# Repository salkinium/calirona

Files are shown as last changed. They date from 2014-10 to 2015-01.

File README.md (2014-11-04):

# Calirona: A calibration robot for Corona

The [Corona][corona] headphones use a HMC6343 compass for heading information which needs to be calibrated from time to time.
To do this, a robot rotates the headphones around two axis while the compass is in calibration mode.

The main design goals of this project are to:

-	calibrate the compass,
-	minimize the required technical knowledge to operate the robot,
-	test the compass functionality to catch the most obvious malfunctions.

This project was designed and manufactured at [The Media Computing Group][i10].

## Design

The robot can move the headphones around both two axes a full 360°, which are supported using ball bearings. The z-axis uses a dish which holds the headphones.

Since the power and signal lines for the headphones and second axis motor need to be relayed through both axis, the robot cannot rotate infinitely around its axis.  
Therefore two position switches exist, which allow the robot to rotate its axes into known safe positions before attempting a rotation.  
The robot will then rotate 360° around the x-axis, then 360° around the z-axis, and then reverse all rotations until it has reached the starting state again.

The robot is controlled by two buttons Start and Stop, and can display its internal state through leds for power, busy, headphone error and mechanical error.  
The mapping is as follows:

- START: initialize and start the calibration.
- STOP: stop robot movement (short press), release motors and reset robot (long press)
- Busy (blue): blinks, when an operation is in progress, otherwise off
- Headphone (orange): blinks, when no headphone is connected, or it is unresponsive (perhaps broken), otherwise on
- Mechanical Error (red): blinks, when the robot detected an invalid mechanical state (broken or blocked motor), otherwise off

## Usage

The basic usage of the robots is as follows:

1. Plug in the power cord. The green power led should light up and the headphone error led should blink.
2. Place the headphone into the holder drum and plug in the headphone jack. The headphone error led should stop blinking and turn on fully, unless the headphone is broken.
3. Press START. The robot will initialize its axes.
4. Press START again. The robot will do two rotations while calibrating the headphones.
5. Once the robot stopped moving, unplug the now calibrated headphones and remove them.

If the robot detected an invalid state during any of the actions, it will stop moving and blink an error led.

**Press the STOP button anytime to stop the robot from moving!**  
Pressing the STOP button for a longer time resets the robot.

## Organization

This repository is organized as follows:

- 	The *hardware* folder contains all hardware files for the robot.
	-	*hardware/et* contains the PCB schematics and layouts.
	-	*hardware/mech* contains the vector files of all mechanical parts of the robot (for the lasercutter).
- 	The *software* folder contains the software for the robot.
	- 	*software/source* contains the actual application code for this robot.
	-	*software/xpcc* contains the git submodule for the xpcc.io microcontroller framework.

All hardware and embedded software was designed by [Niklas Hauser][hauser].

[i10]: http://hci.rwth-aachen.de
[corona]: http://hci.rwth-aachen.de/corona
[hauser]: http://hci.rwth-aachen.de/hauser

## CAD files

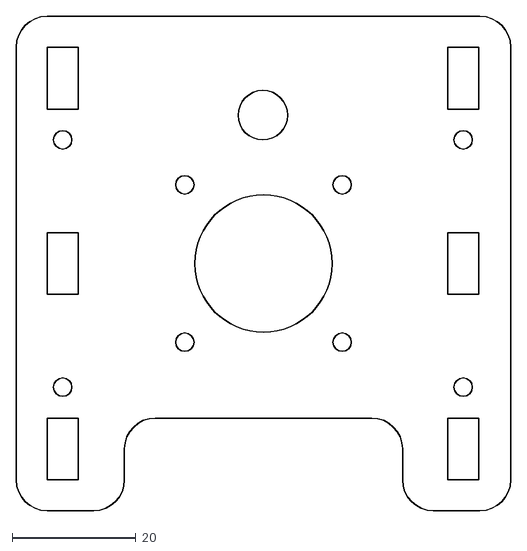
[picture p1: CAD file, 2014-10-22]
hardware/mech/gears_x_large_without_gear_5mm.dxf
80.0 x 80.0

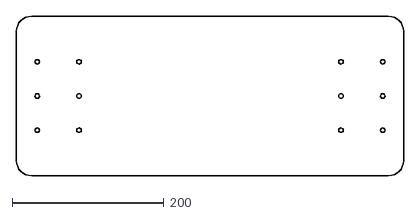
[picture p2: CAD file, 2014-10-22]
hardware/mech/base_large.dxf
510.0 x 210.0

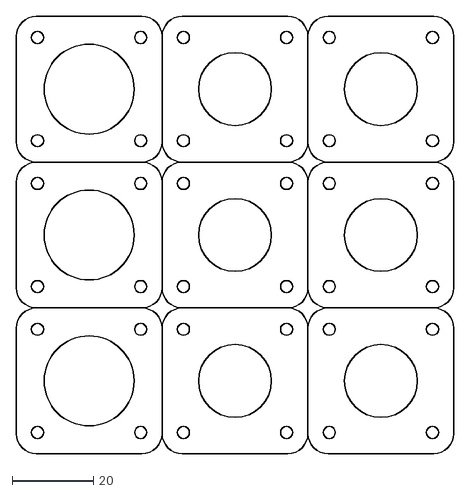
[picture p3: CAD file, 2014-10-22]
hardware/mech/gears_z_center_bearing_holder_2mm.dxf
108.0 x 108.0

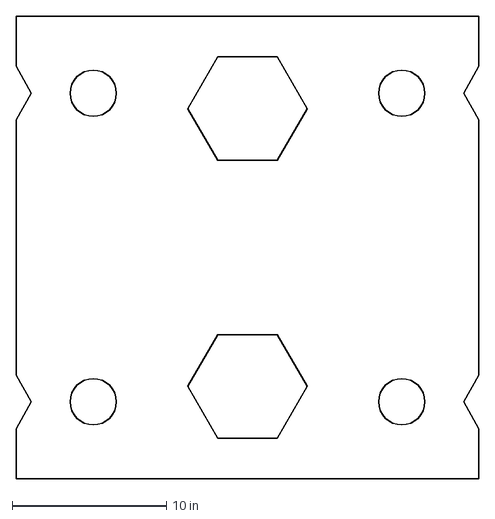
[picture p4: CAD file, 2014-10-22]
hardware/mech/rotation_arm_side_holder_bearings_upper.dxf
30.0 x 30.0 in

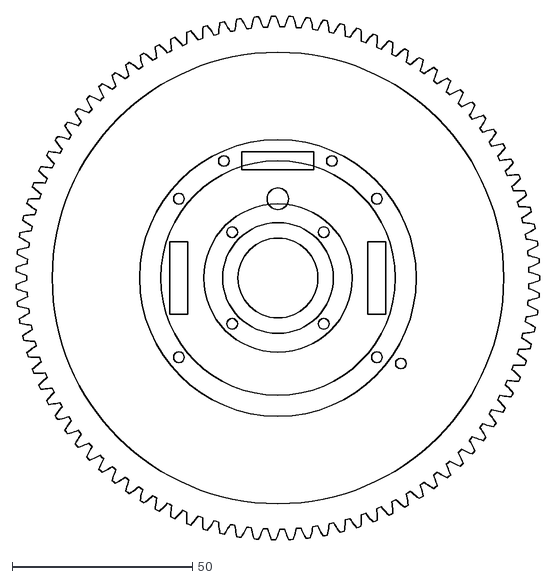
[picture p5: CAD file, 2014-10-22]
hardware/mech/gears_z_large_5mm.dxf
145.5 x 145.5

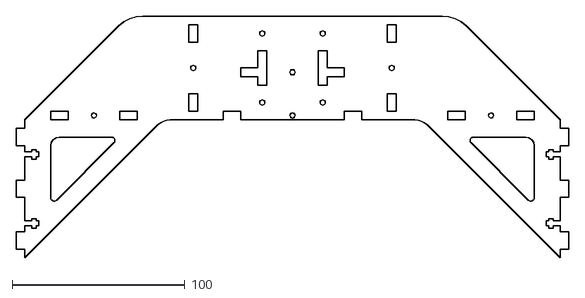
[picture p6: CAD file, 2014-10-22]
hardware/mech/rotation_arm.dxf
320.0 x 140.0

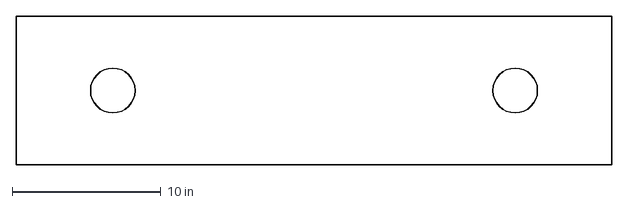
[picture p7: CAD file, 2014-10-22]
hardware/mech/rectphones.dxf
40.0 x 10.0 in

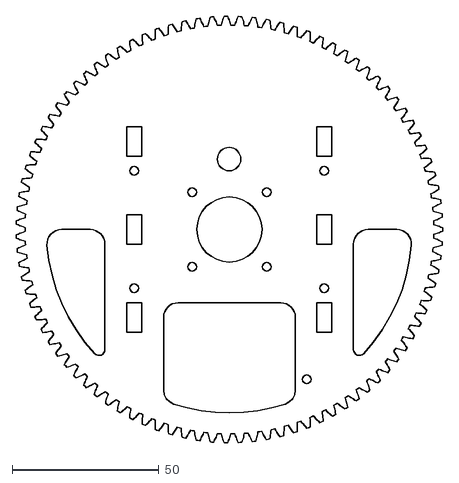
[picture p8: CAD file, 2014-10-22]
hardware/mech/gears_x_large_5mm.dxf
145.5 x 145.5

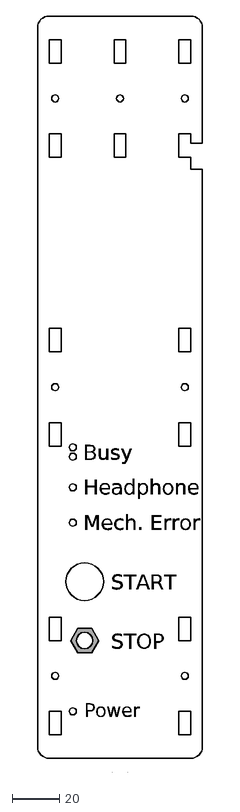
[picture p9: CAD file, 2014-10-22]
hardware/mech/arm_side_structure_LEDs.dxf
Power
Mech. Error
Headphone
Busy
START
STOP

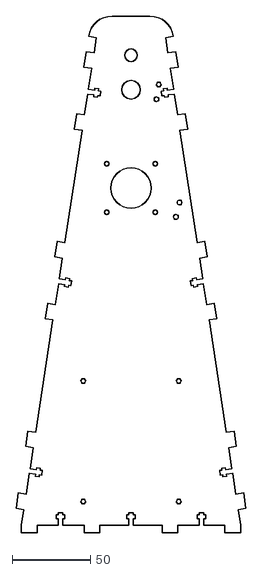
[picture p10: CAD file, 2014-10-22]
hardware/mech/arm_structure_motor.dxf
146.8 x 330.0

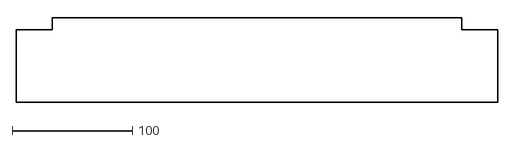
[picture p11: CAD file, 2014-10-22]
hardware/mech/holder_drum_circumfence.dxf
400.0 x 70.0

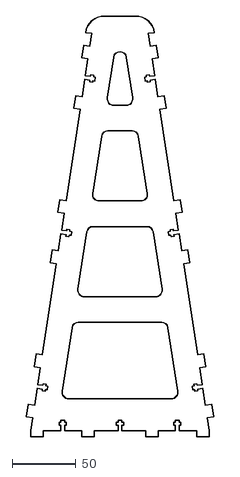
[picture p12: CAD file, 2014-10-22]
hardware/mech/arm_structure.dxf
146.8 x 330.0

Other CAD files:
hardware/mech/rotation_arm_side_holder_stabilizer.dxf
hardware/mech/holder_drum_bottom_5mm.dwg
hardware/mech/arm_axis_middle.dxf
hardware/mech/rotation_arm_side_holder.dxf
hardware/mech/holder_vertical_5mm.dwg
hardware/mech/holder_drum_top_5mm.dxf
hardware/mech/arm_axis_middle.dwg
hardware/mech/arm_side_structure.dwg
hardware/mech/arm_side_structure.dxf
hardware/mech/arm_side_structure_LEDs.dwg
hardware/mech/arm_structure.dwg
hardware/mech/arm_structure_axis.dwg
hardware/mech/arm_structure_axis.dxf
hardware/mech/arm_structure_motor.dwg
hardware/mech/base_large.dwg
hardware/mech/base_small.dwg
hardware/mech/base_small.dxf
hardware/mech/gears_x_large_5mm.dwg
hardware/mech/gears_x_large_without_gear_5mm.dwg
hardware/mech/gears_z_center_bearing_holder_2mm.dwg
hardware/mech/gears_z_large_5mm.dwg
hardware/mech/gears_z_small_5mm.dwg
hardware/mech/gears_z_small_5mm.dxf
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

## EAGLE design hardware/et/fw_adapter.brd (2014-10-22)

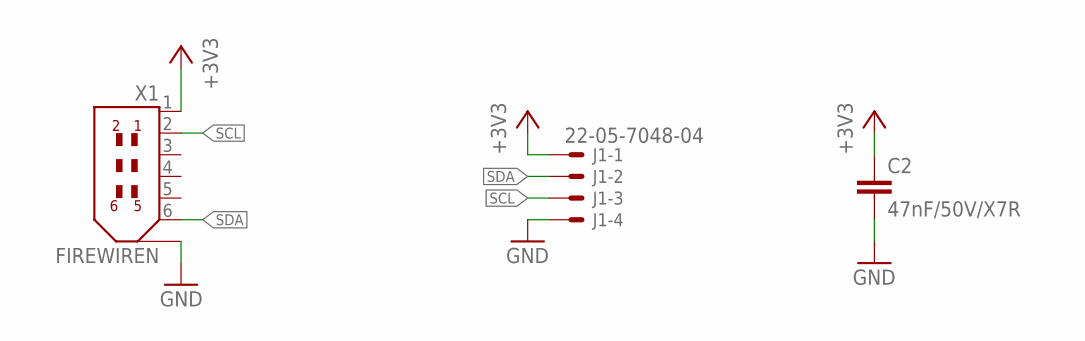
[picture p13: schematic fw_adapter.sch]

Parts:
C2: 47nF/50V/X7R; C0603K
J1: 22-05-7048-04; 7395-04
X1: FIREWIREN; IEEE1394_90DEG_PINS_NORMAL

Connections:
+3V3: C2.1, J1.1, X1.1
GND: C2.2, J1.4, X1.M1 (7), X1.M2 (7)
SCL: J1.3, X1.2
SDA: J1.2, X1.6

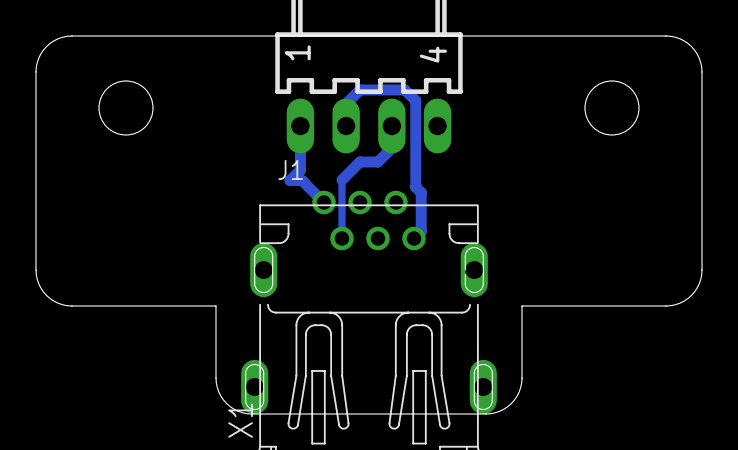
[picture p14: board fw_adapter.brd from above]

Board: 2 copper layers, 37.0 x 21.0 mm, 3 parts (1 on the bottom side), 4 nets.

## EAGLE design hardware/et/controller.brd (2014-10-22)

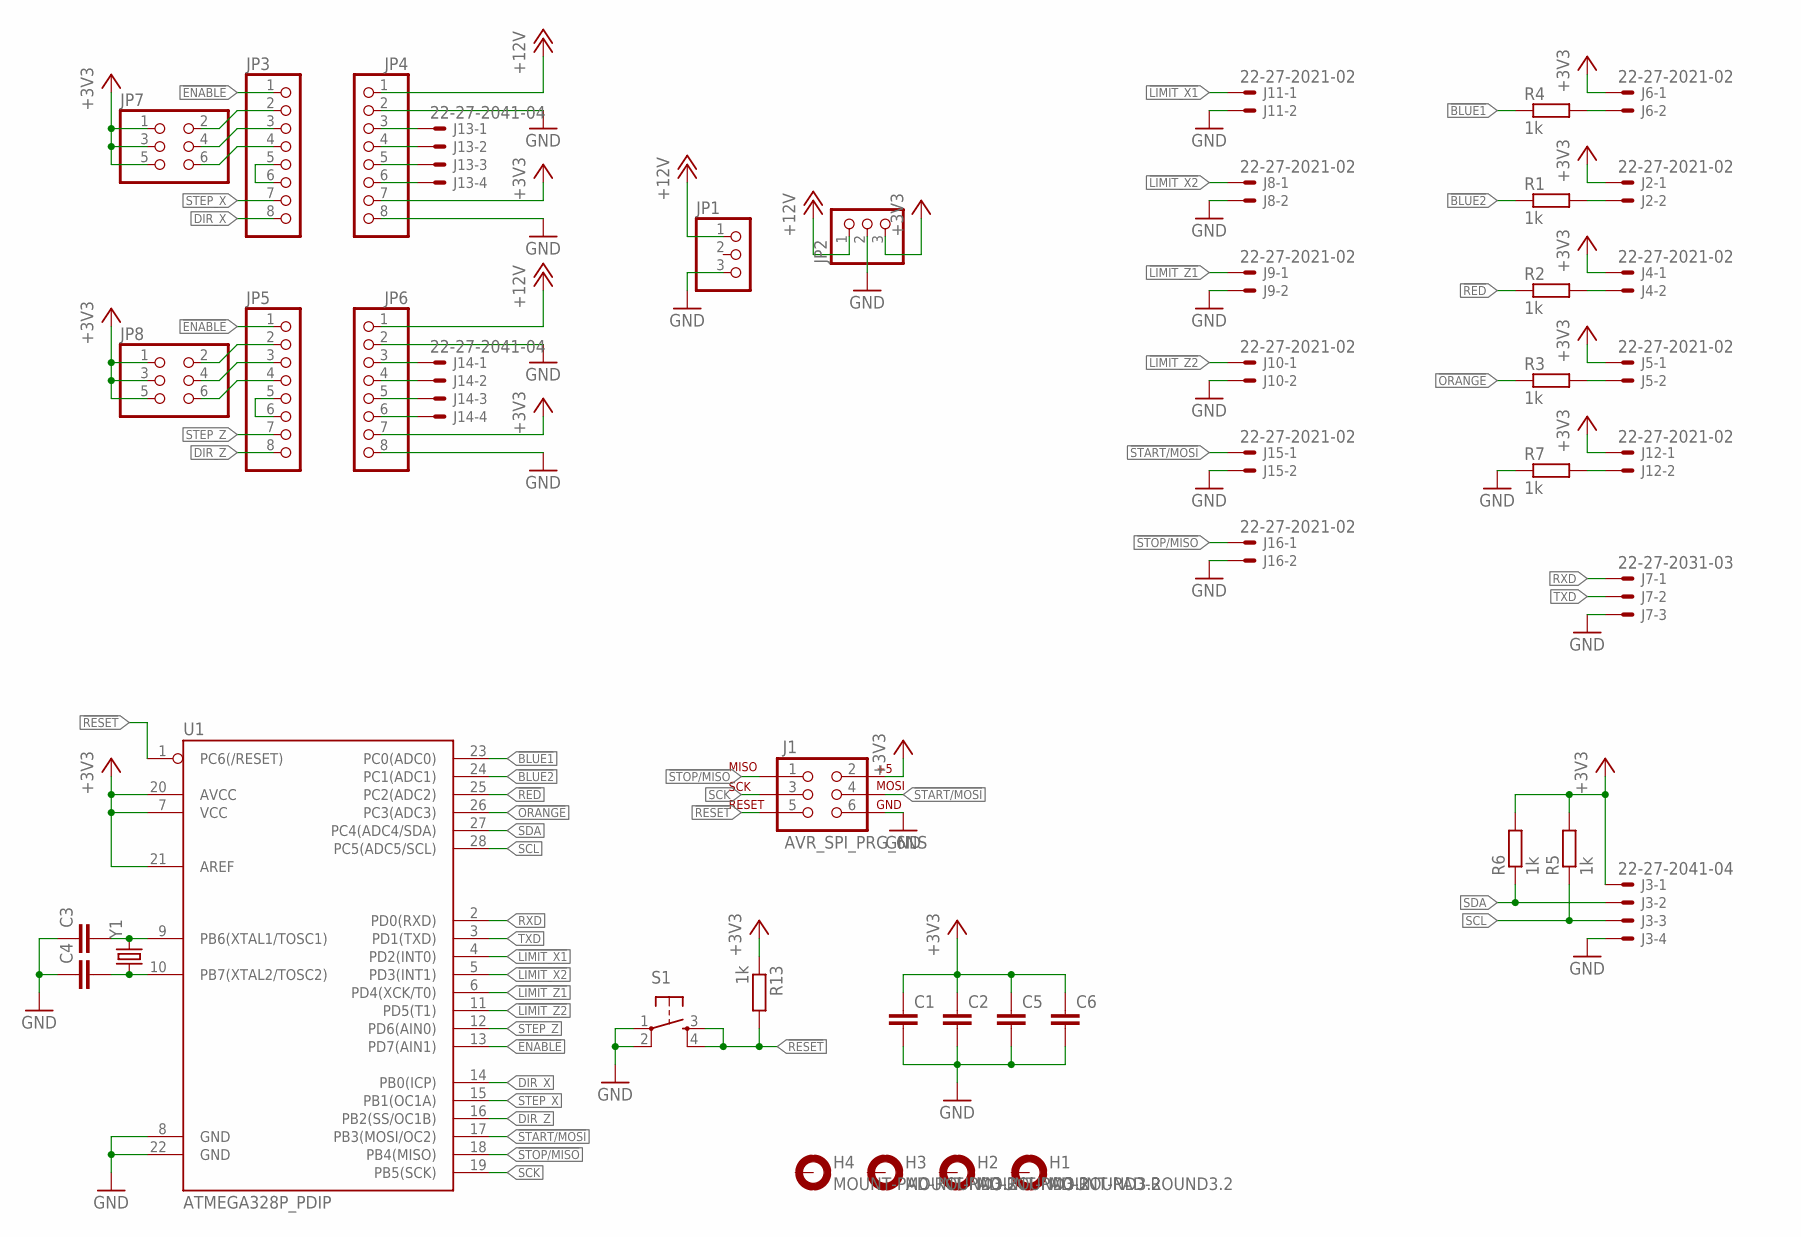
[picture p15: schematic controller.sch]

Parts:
C1, C2, C5, C6: C-EUC0603; C0603
C3, C4: C-EUC0603K; C0603K
H1, H2, H3, H4: MOUNT-PAD-ROUND3.2; 3,2-PAD
J1: AVR_SPI_PRG_6NS; 2X3-NS
J2, J4, J5, J6, J8, J9, J10, J11, J12, J15, J16: 22-27-2021-02; 6410-02
J3, J13, J14: 22-27-2041-04; 6410-04
J7: 22-27-2031-03; 6410-03
JP1, JP2: PINHD-1X3; 1X03
JP3, JP4, JP5, JP6: PINHD-1X8; 1X08
JP7, JP8: PINHD-2X3; 2X03
R1, R2, R3, R4, R5, R6, R7, R13: 1k; R0603
S1: TAC_SWITCHPTH; TACTILE-PTH
U1: ATMEGA328P_PDIP; DIL28-3
Y1: CRYSTALHC49UV; HC49U-V

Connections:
!BLUE1: R4.1, U1.23 (PC0(ADC0))
!BLUE2: R1.1, U1.24 (PC1(ADC1))
!ENABLE: JP3.1, JP5.1, U1.13 (PD7(AIN1))
!LIMIT_X1: J11.1, U1.4 (PD2(INT0))
!LIMIT_X2: J8.1, U1.5 (PD3(INT1))
!LIMIT_Z1: J9.1, U1.6 (PD4(XCK/T0))
!LIMIT_Z2: J10.1, U1.11 (PD5(T1))
!ORANGE: R3.1, U1.26 (PC3(ADC3))
!RED: R2.1, U1.25 (PC2(ADC2))
!RESET: J1.5, R13.2, S1.3, S1.4, U1.1 (PC6(/RESET))
!START/MOSI: J1.4, J15.1, U1.17 (PB3(MOSI/OC2))
!STOP/MISO: J1.1, J16.1, U1.18 (PB4(MISO))
+3V3: C1.1, C2.1, C5.1, C6.1, J1.2, J2.1, J3.1, J4.1, J5.1, J6.1, J12.1, JP2.3, JP4.7, JP6.7, JP7.1, JP7.3, JP7.5, JP8.1, JP8.3, JP8.5, R5.2, R6.2, R13.1, U1.7 (VCC), U1.20 (AVCC), U1.21 (AREF)
+12V: JP1.1, JP2.1, JP4.1, JP6.1
DIR_X: JP3.8, U1.14 (PB0(ICP))
DIR_Z: JP5.8, U1.16 (PB2(SS/OC1B))
GND: C1.2, C2.2, C3.1, C4.1, C5.2, C6.2, J1.6, J3.4, J7.3, J8.2, J9.2, J10.2, J11.2, J15.2, J16.2, JP1.3, JP2.2, JP4.2, JP4.8, JP6.2, JP6.8, R7.1, S1.1, S1.2, U1.8 (GND), U1.22 (GND)
unnamed: C3.2, U1.9 (PB6(XTAL1/TOSC1)), Y1.2
unnamed: C4.2, U1.10 (PB7(XTAL2/TOSC2)), Y1.1
unnamed: J4.2, R2.2
unnamed: J2.2, R1.2
unnamed: J5.2, R3.2
unnamed: J6.2, R4.2
unnamed: JP3.5, JP3.6
unnamed: JP3.4, JP7.6
unnamed: JP3.3, JP7.4
unnamed: JP3.2, JP7.2
unnamed: J12.2, R7.2
unnamed: JP5.5, JP5.6
unnamed: JP5.4, JP8.6
unnamed: JP5.3, JP8.4
unnamed: JP5.2, JP8.2
unnamed: J13.1, JP4.3
unnamed: J13.2, JP4.4
unnamed: J13.3, JP4.5
unnamed: J13.4, JP4.6
unnamed: J14.1, JP6.3
unnamed: J14.2, JP6.4
unnamed: J14.3, JP6.5
unnamed: J14.4, JP6.6
RXD: J7.1, U1.2 (PD0(RXD))
SCK: J1.3, U1.19 (PB5(SCK))
SCL: J3.3, R5.1, U1.28 (PC5(ADC5/SCL))
SDA: J3.2, R6.1, U1.27 (PC4(ADC4/SDA))
STEP_X: JP3.7, U1.15 (PB1(OC1A))
STEP_Z: JP5.7, U1.12 (PD6(AIN0))
TXD: J7.2, U1.3 (PD1(TXD))

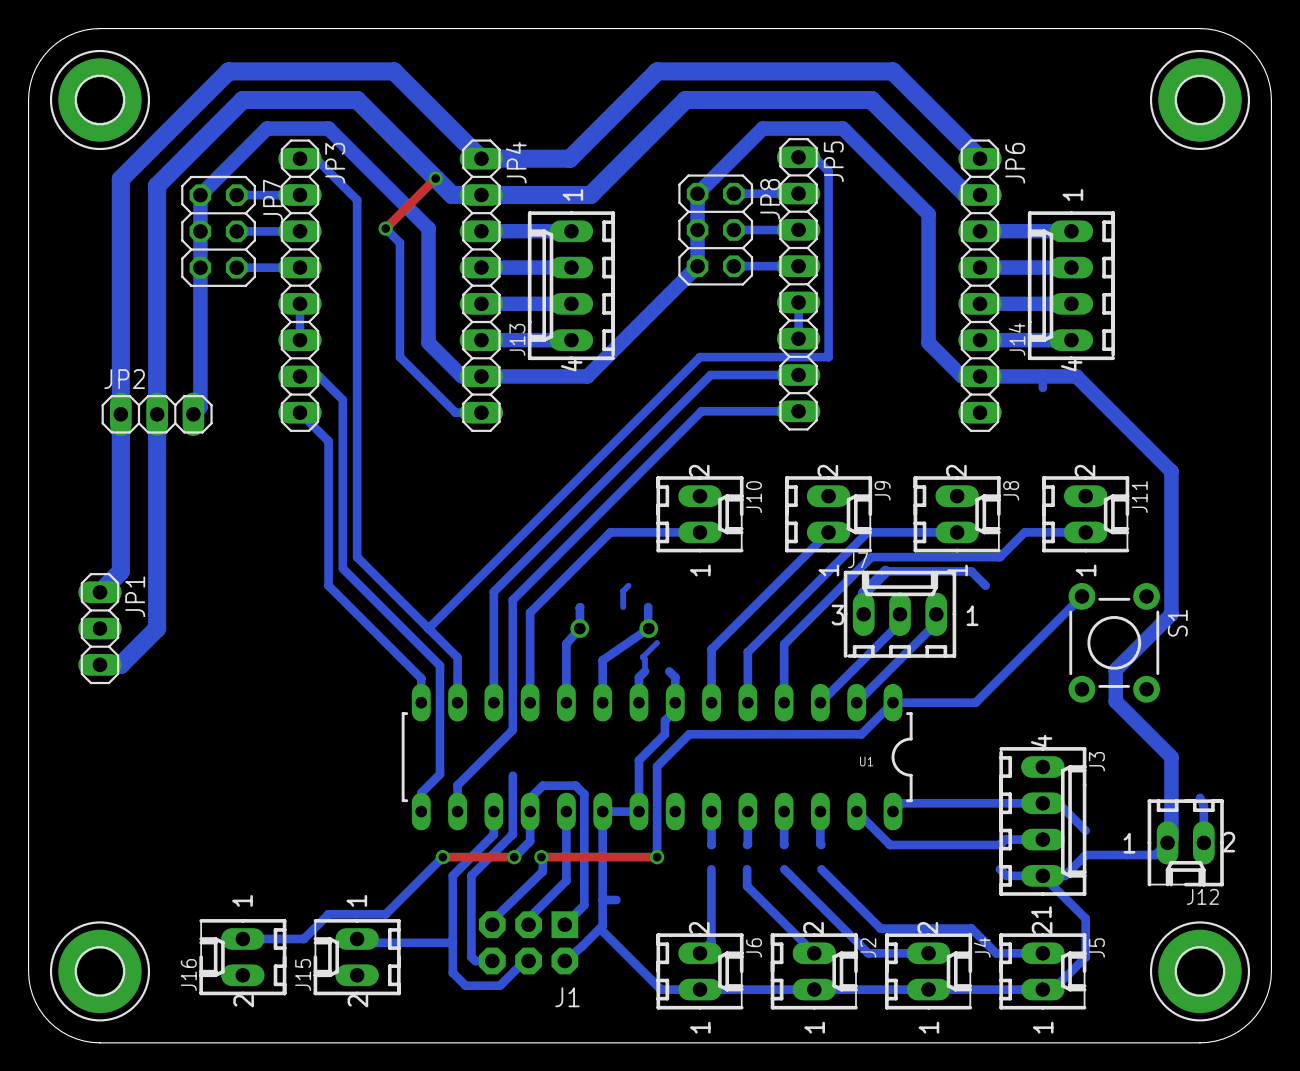
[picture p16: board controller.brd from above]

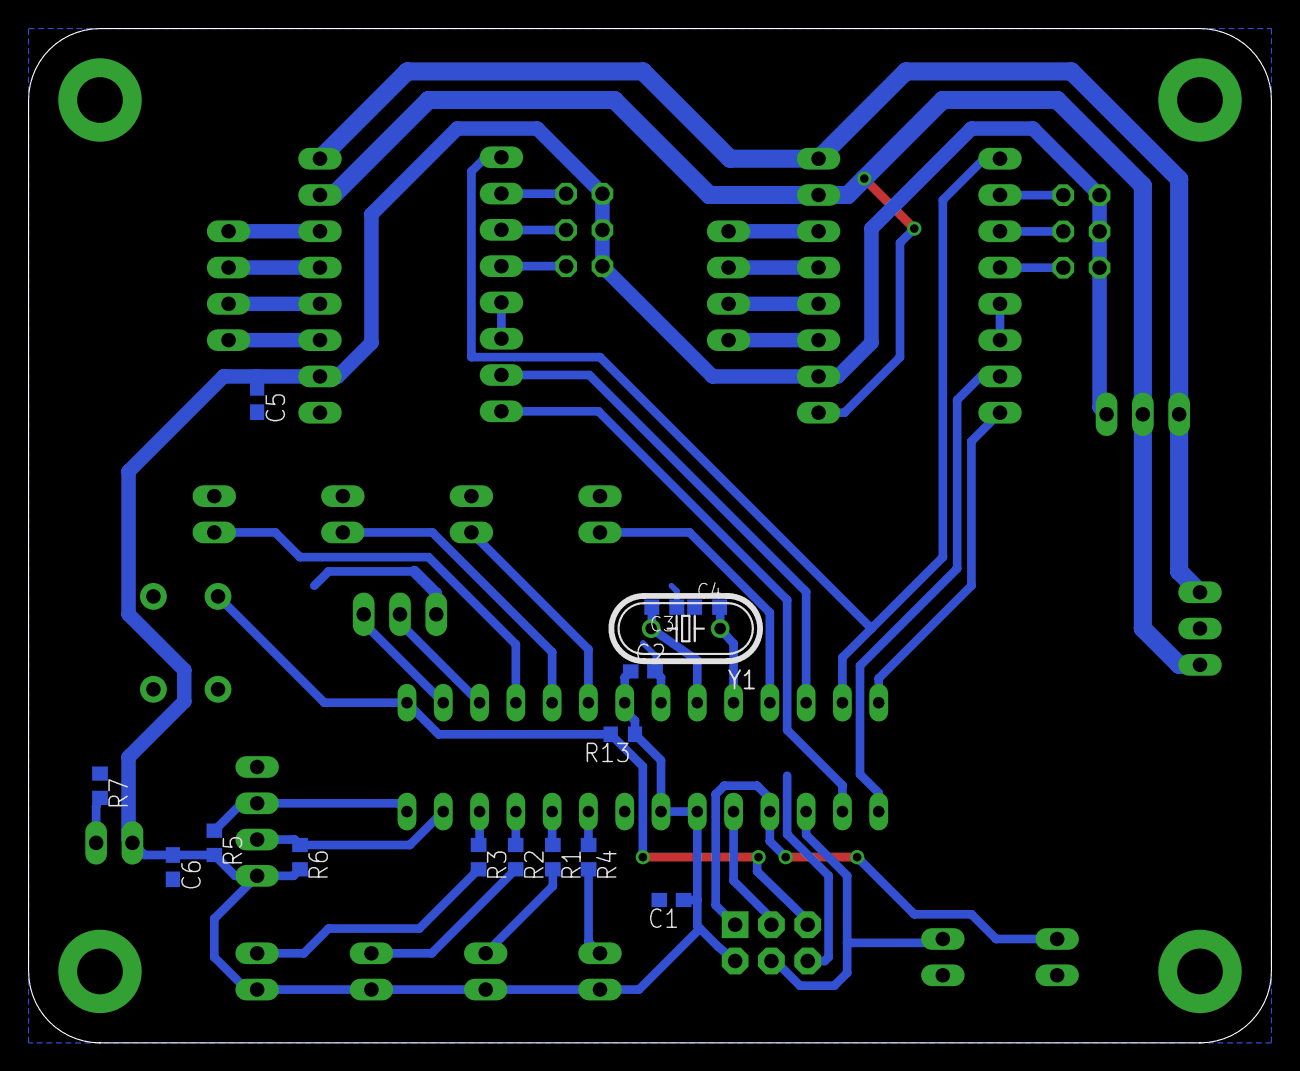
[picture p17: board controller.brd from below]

Board: 2 copper layers, 87.0 x 71.0 mm, 45 parts (15 on the bottom side), 47 nets.

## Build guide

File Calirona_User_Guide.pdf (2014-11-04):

# Calirona Benutzeranleitung

1. Klemme den Kopfhörer auf den Halter, wickle das Kabel herum und stecke es in die Buchse.
Drücke den Halter währenddessen nicht von dir weg!
Die Headphone LED hört auf zu blinken, wenn der Kopfhörer erkannt wurde.
2. Drücke START. Der Roboter initialisiert seine Achsen.
3. Drücke wieder START. Der Roboter dreht sich zwei Mal um seine Achsen, während er den Kopfhörer kalibriert.
4. Sobald der Roboter seine Bewegung beendet hat, ziehe den Stecker aus der Buchse und entferne den jetzt kalibrierten Kopfhörer.

Drücke STOP jederzeit um den Roboter zu stoppen!
Drücke STOP länger um den Roboter zurück zu setzen.

Falls der Roboter ein mechanisches Problem entdeckt, hört er auf sich zu bewegen und lässt die Mech. Error LED blinken.
Der Roboter wird weitere Aktionen verweigern, um sich nicht selbst zu beschädigen.

# Calirona User Guide

1. Place the headphone onto the holder, wrap the cable around it and plug in the headphone jack.
Do not push the holder away from you during this action!
The Headphone led stops blinking when the headphone has been detected.
2. Press START. The robot initializes its axes.
3. Press START again. The robot rotates twice around its axis while calibrating the headphones.
4. Once the robot stopped moving, unplug the now calibrated headphones and remove them.

Press the STOP button anytime to stop the robot from moving!
Pressing the STOP button for a longer time resets the robot.

If the robot detected an invalid mechanical state during any of the actions, it will stop moving and blink its Mech. Error led.
The robot will refuse execution of further actions to prevent damaging itself.

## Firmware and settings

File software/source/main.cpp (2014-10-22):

// coding: utf-8
#include "hardware.hpp"
// INTERRUPTS #################################################################
ISR(TIMER2_COMPA_vect)
{
	xpcc::Clock::increment();
}

ISR(TIMER0_COMPA_vect)
{
	t0_steps++;
}

ISR(TIMER1_COMPA_vect)
{
	t1_steps++;
}

MAIN_FUNCTION
{
	// Initiate 1kHz interrupt for clock using Timer2
	// Clear Timer on Compare Match (CTC) Mode
	TCCR2A = (1 << WGM21);
	// 1kHz (= 11059.2kHz / 64 / 173)
	OCR2A = 173;
	// Prescaler 64, enable Timer2
	TCCR2B = (1 << CS22);
	// Enable Overflow Interrupt
	TIMSK2 = (1 << OCIE2A);

	leds.initialize();
	buttons.initialize();
	mechanics.initialize();
	manager.initialize();

	Scl::connect(Twi::Scl);
	Sda::connect(Twi::Sda);
	Twi::initialize<systemClock, Twi::Baudrate::Standard>();

	GpioD0::connect(Uart::Rx);
	GpioD1::connect(Uart::Tx);
	Uart::initialize<systemClock, Uart::B115200>();

	xpcc::atmega::enableInterrupts();

	XPCC_LOG_INFO << "RESTART" << xpcc::endl;

	while (1)
	{
		buttons.update();
		leds.update();
		headphone.update();
		mechanics.update();
		manager.update();
	}

//	return 0;
}

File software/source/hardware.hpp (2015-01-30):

// coding: utf-8
/* Copyright (c) 2014, Niklas Hauser
* All Rights Reserved.
*/
// ----------------------------------------------------------------------------

#ifndef CALIRONA_HARDWARE
#define CALIRONA_HARDWARE

#include <xpcc/architecture/platform.hpp>

using namespace xpcc::atmega;

// IO #########################################################################
// ATMEL ATMEGA328P
//                     +-v-+
//      (!RESET) PC6  1|   |28  PC5 (SCL)
//         (RXD) PD0  2|   |27  PC4 (SDA)
//         (TXD) PD1  3|   |26  PC3 (!HEADPHONE)
//   (!X_LIMIT1) PD2  4|   |25  PC2 (!MECH_ERROR)
//   (!X_LIMIT2) PD3  5|   |24  PC1 (!BUSY2)
//   (!Z_LIMIT1) PD4  6|   |23  PC0 (!BUSY1)
//               VCC  7|   |22  GND
//               GND  8|   |21  AREF
//       (XTAL1) PB6  9|   |20  AVCC
//       (XTAL2) PB7 10|   |19  PB5 (SCK)
//   (!Z_LIMIT2) PD5 11|   |18  PB4 (!START/MISO)
// (Z_STEP/OC0A) PD6 12|   |17  PB3 (!STOP/MOSI)
//     (!ENABLE) PD7 13|   |16  PB2 (Z_DIR)
//       (X_DIR) PB0 14|   |15  PB1 (X_STEP/OC1A)
//                     +---+

typedef xpcc::avr::SystemClock systemClock;

// motor step counters
uint16_t t0_steps;
uint16_t t1_steps;

// Motors
typedef xpcc::GpioInverted< GpioOpenDrain< GpioD7 > > XZ_Enable;

// X-Axis
typedef xpcc::GpioInverted< GpioInputD2 > X_Limit1;
typedef xpcc::GpioInverted< GpioInputD3 > X_Limit2;
typedef GpioOutputB0 X_Dir;
typedef GpioOutputB1 X_Step;

// Z-Axis
typedef xpcc::GpioInverted< GpioInputD4 > Z_Limit1;
typedef xpcc::GpioInverted< GpioInputD5 > Z_Limit2;
typedef GpioOutputB2 Z_Dir;
typedef GpioOutputD6 Z_Step;

// LEDs
typedef xpcc::GpioInverted< GpioOutputC0 > LED_Busy1;
typedef xpcc::GpioInverted< GpioOutputC1 > LED_Busy2;
typedef xpcc::GpioInverted< GpioOutputC2 > LED_Headphone;
typedef xpcc::GpioInverted< GpioOutputC3 > LED_MechError;

// Buttons
typedef xpcc::GpioInverted< GpioInputB4 > ButtonStart;
typedef xpcc::GpioInverted< GpioInputB3 > ButtonStop;

// COMMUNICATION ##############################################################
typedef GpioC4 Sda;
typedef GpioC5 Scl;
typedef I2cMaster Twi;

// SERIAL DEBUG ###############################################################
#include <xpcc/io/iodevice_wrapper.hpp>
typedef Uart0 Uart;
xpcc::IODeviceWrapper< Uart, xpcc::IOBuffer::BlockIfFull > outputDevice;

#include <xpcc/debug/logger/style_wrapper.hpp>
#include <xpcc/debug/logger/style/prefix.hpp>
#include <xpcc/debug/logger.hpp>
xpcc::log::StyleWrapper< xpcc::log::Prefix< char[10] > > loggerDeviceDebug (
		xpcc::log::Prefix< char[10] > ("Debug:   ", outputDevice ) );
xpcc::log::Logger xpcc::log::debug( loggerDeviceDebug );

xpcc::log::StyleWrapper< xpcc::log::Prefix< char[10] > > loggerDeviceInfo (
		xpcc::log::Prefix< char[10] > ("Info:    ", outputDevice ) );
xpcc::log::Logger xpcc::log::info( loggerDeviceInfo );

xpcc::log::StyleWrapper< xpcc::log::Prefix< char[10] > > loggerDeviceWarning (
		xpcc::log::Prefix< char[10] > ("Warning: ", outputDevice ) );
xpcc::log::Logger xpcc::log::warning( loggerDeviceWarning );

xpcc::log::StyleWrapper< xpcc::log::Prefix< char[10] > > loggerDeviceError (
		xpcc::log::Prefix< char[10] > ("Error:   ", outputDevice ) );
xpcc::log::Logger xpcc::log::error( loggerDeviceError );

#undef	XPCC_LOG_LEVEL
#define	XPCC_LOG_LEVEL xpcc::log::DEBUG

// TASKS ######################################################################
#include "tasks/task_buttons.hpp"
task::Buttons buttons;
#include "tasks/task_leds.hpp"
task::Leds leds;

#include "tasks/task_headphone.hpp"
task::Headphone headphone(leds);

#include "tasks/task_mechanics.hpp"
task::Mechanics mechanics(leds, buttons);

#include "tasks/task_manager.hpp"
task::Manager manager(buttons, leds, headphone, mechanics);

#endif // CALIRONA_HARDWARE

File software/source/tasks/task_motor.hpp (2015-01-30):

// coding: utf-8
/* Copyright (c) 2013, Roboterclub Aachen e.V.
 * All Rights Reserved.
 *
 * The file is part of the xpcc library and is released under the 3-clause BSD
 * license. See the file `LICENSE` for the full license governing this code.
 */
// ----------------------------------------------------------------------------

#ifndef TASK_A4988_HPP
#define TASK_A4988_HPP

#include <xpcc/architecture/utils.hpp>
#include <xpcc/processing/timeout.hpp>
#include <xpcc/debug/logger.hpp>

#undef	XPCC_LOG_LEVEL
#define	XPCC_LOG_LEVEL xpcc::log::INFO

namespace task
{

/**
 * A4988 stepper motor driver.
 *
 * @author	Niklas Hauser
 */
template< typename Direction, typename Step, uint16_t MotorSteps >
class Motor
{
public:
	Motor(volatile uint8_t *compare, volatile uint8_t *prescaler, uint16_t &steps)
	:	mode(MODE_OFF), compare(compare), prescaler(prescaler), steps(steps)
	{
		stopTimer();
		steps = 0;
	}

	void
	initialize()
	{
		Direction::setOutput(xpcc::Gpio::Low);
		Step::setOutput(xpcc::Gpio::Low);
	}

	bool
	setSpeed(int16_t deciDegreesPerSecond);

	bool
	rotateBy(int16_t deciDegrees, uint16_t milliSeconds);

	void
	stop()
	{
		stopTimer();
		mode = MODE_OFF;
		Step::reset();
		steps = 0;
	}

	bool inline
	isRunning()
	{
		return (mode > MODE_OFF);
	}

	void
	update();

private:
	void inline
	stopTimer()
	{
		*prescaler &= ~0b111;
	}

	void inline
	startTimer()
	{
		// Prescaler 1024
		// horrible hack, just horrible.
		if (prescaler == &TCCR0B) TCNT0 = 0;
		else TCNT1 = 0;
		*prescaler |= 0b101;
	}

	void inline
	setTimerSpeed(uint8_t speed)
	{
		if (speed == 0) speed = 1;
		*compare = speed;
		XPCC_LOG_DEBUG << "speed = " << speed << xpcc::endl;
	}

	enum
	{
		MODE_OFF = 0,
		MODE_SPEED = 1,
		MODE_ANGLE = 2
	};
	volatile uint8_t mode;
	uint16_t required_steps;

	volatile uint8_t *compare;
	volatile uint8_t *prescaler;
	uint16_t &steps;
};

}	// namespace task

#include "task_motor_impl.hpp"

#endif // TASK_A4988_HPP

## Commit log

2013-08-24 Initial commit.
    [project.cfg]
2013-08-29 Add A4988 stepper motor driver. Update xpcc.
2013-08-30 Add Rotate Task without I2c control yet. Move hardware definitions into own file.
2013-08-30 Fix timer init, xpcc::Clock was running twice as fast.
    [main.cpp]
2013-09-22 Add manager task. Add debounced start and stop buttons. Update xpcc.io.
2013-09-24 Software: Add Logger output. Fix I2c problems.
    [hardware.hpp, main.cpp]
2013-10-01 Software: Move Dir and Step pins of Z axis. Add code to stop Motors, when stop button is pressed. Update xpcc.io.
    [project.cfg]
2014-09-24 Update software.
    [project.cfg]
2014-10-21 Increase uart buffer through xpcc parameter magic.
    [project.cfg]
2014-10-21 Fix motor problems with time tracking by simply counting the steps.
    [hardware.hpp, main.cpp, task_motor.hpp]
2014-10-21 Add timeout to Mechanics class to release the motors after 30s.
2014-10-21 Manager class now handles the basic calibration and rotation tasks.
2014-10-22 Add PCB schematics and layouts.
    [controller.brd, controller.sch, fw_adapter.brd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]
2014-10-22 Add all hardware files for the robot’s structure.
    [arm_axis_middle.dwg, arm_axis_middle.dxf, arm_side_structure.dwg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]
2014-10-22 Set IIR Filter to 5.
2014-10-22 Invert Headphone Led behaviour.
2014-10-22 Reduce calibration timeout, to limit mechanical damage by overdrawn limit switch.
2014-10-22 Move remaining button code from main loop to manager task.
2014-10-27 Make Calibrate task a little safer.
2014-11-03 Adapt for a change in x-axis end switch position.
2014-11-04 Fix reset of mech error leds before it was triggered.
    [hardware.hpp]

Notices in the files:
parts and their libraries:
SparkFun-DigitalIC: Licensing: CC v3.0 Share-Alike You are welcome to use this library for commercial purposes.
